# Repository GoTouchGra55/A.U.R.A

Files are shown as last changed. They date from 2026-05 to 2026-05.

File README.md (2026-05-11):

# 🚧 Under Active Development 🚧

# 

### A **flight computer** to do met- I mean math for a **rocket** (*Supposedly for a self-landing rocket*).

I had a lot of fun designing this project, though there may still be a few mistakes here and there, so forgive me for that

Feel free to suggest improvements, modify the design, or contribute your own ideas to the project as well!

---

# PCB Preview

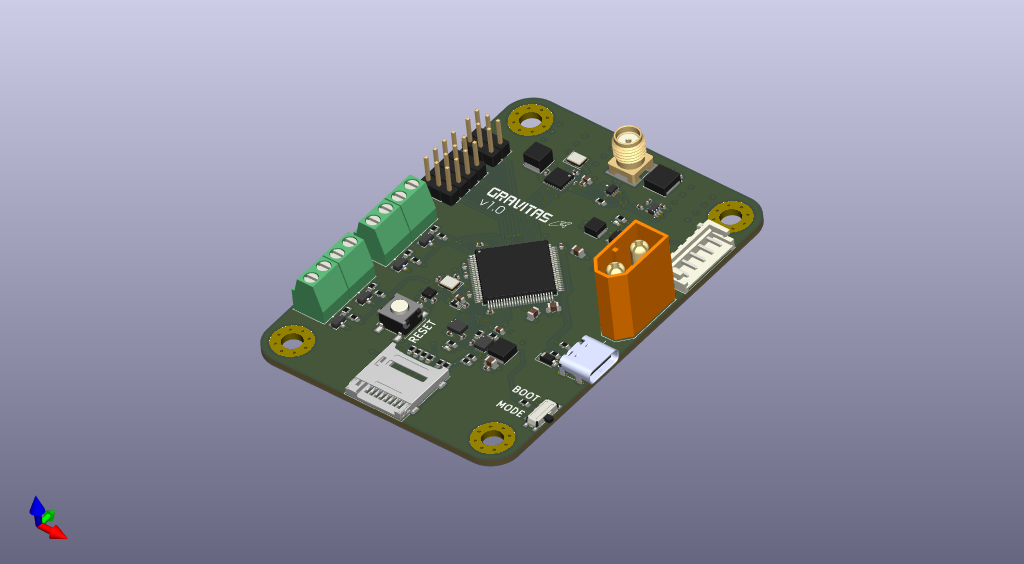
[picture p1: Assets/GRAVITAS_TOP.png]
PCB_TOP


### Yes, its 4 layers ;3

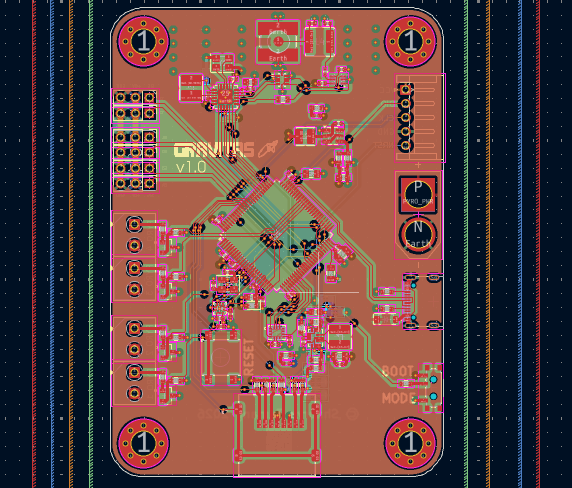
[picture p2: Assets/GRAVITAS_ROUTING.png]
PCB_ROUTES


---

# Schematics
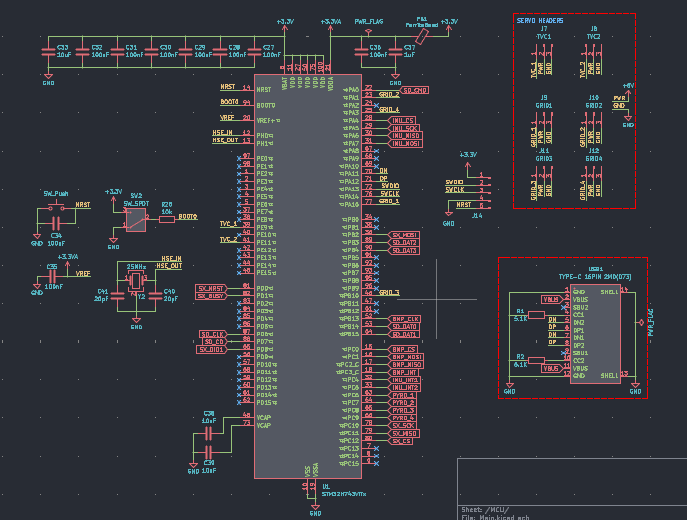
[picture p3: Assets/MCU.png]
MAIN

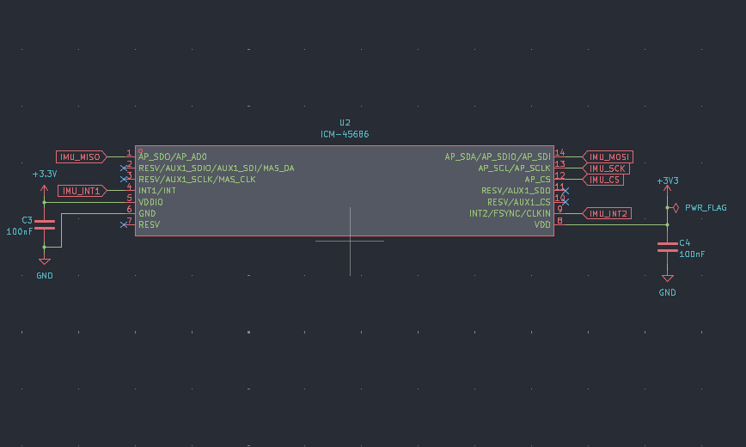
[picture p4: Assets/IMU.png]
IMU

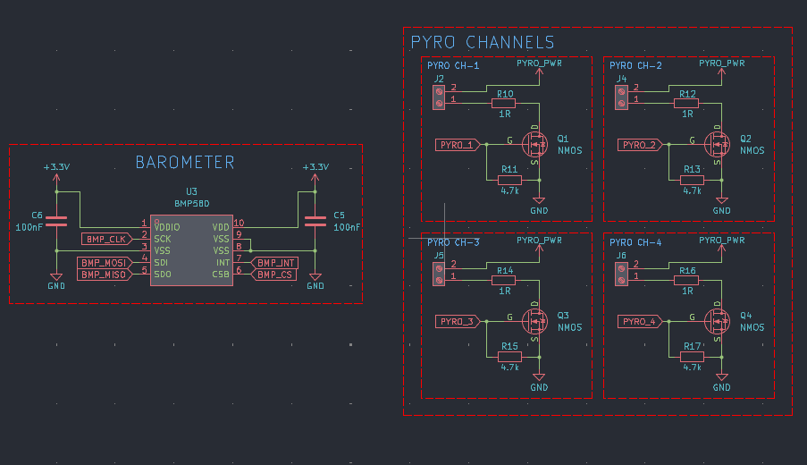
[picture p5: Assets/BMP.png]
BMP

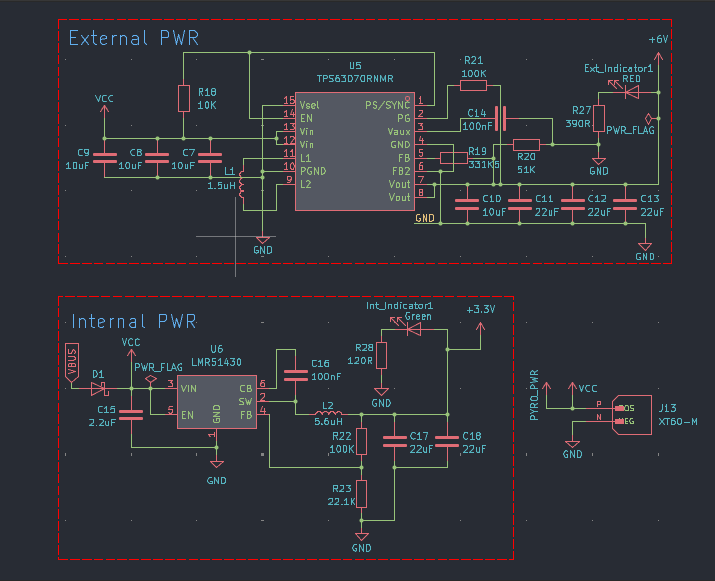
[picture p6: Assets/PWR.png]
PWR

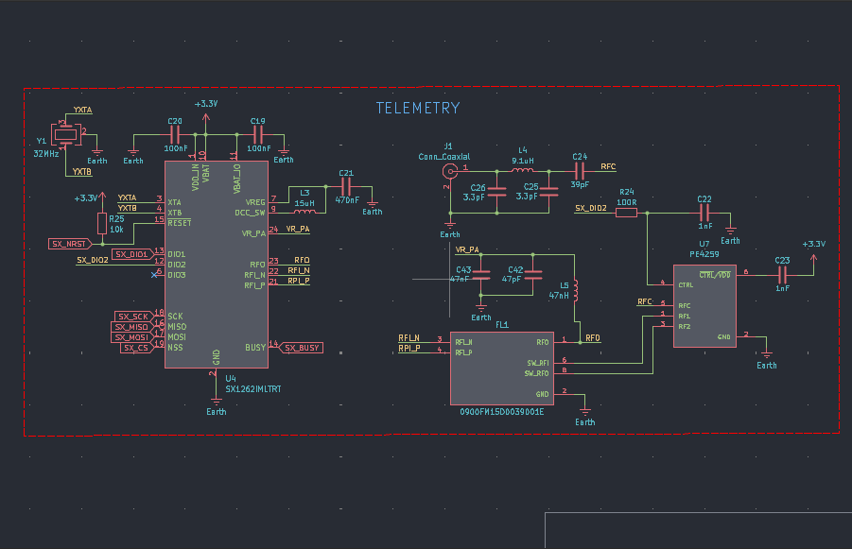
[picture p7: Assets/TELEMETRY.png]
TELEMETRY

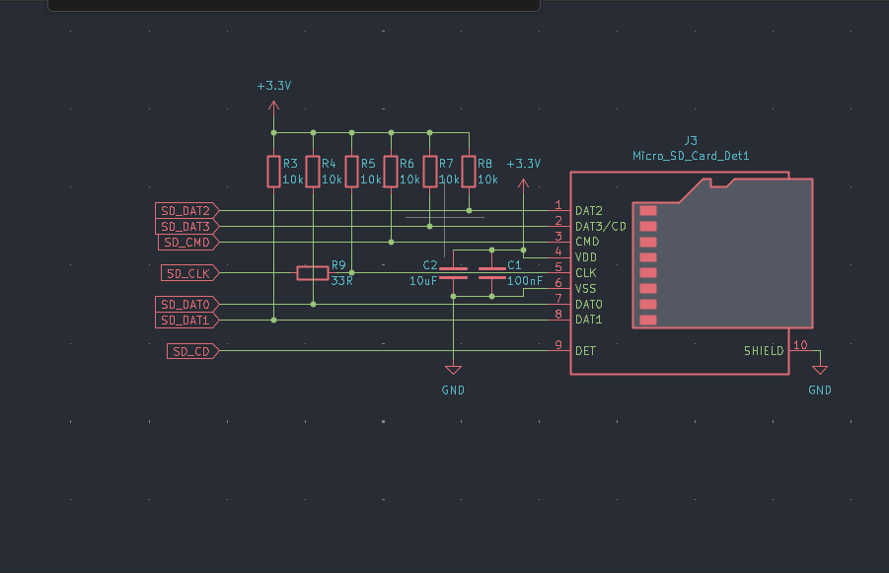
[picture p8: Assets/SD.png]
SD


---

# Extra Info

1. **Use a 2s LiPo battery** if you decide to use this board in your project. **Discard the battery if it smells "funny".**

2. **Check for any damage on the pcb** as it can be the reason for a **catastrophic failure**.

3. **USE A 915MHz SMA ANTENNA ONLY!** Others will work fine but you'll spend a while wondering about the poor range.

---

# Bill Of Materials

### See [BOM](Gravitas-bom.csv)

---

# License

### MIT License - see [LICENSE](LICENSE)

---

# Author

### **Shaurya Tamang**
Contact: shauryatamang.dev@gmail.com

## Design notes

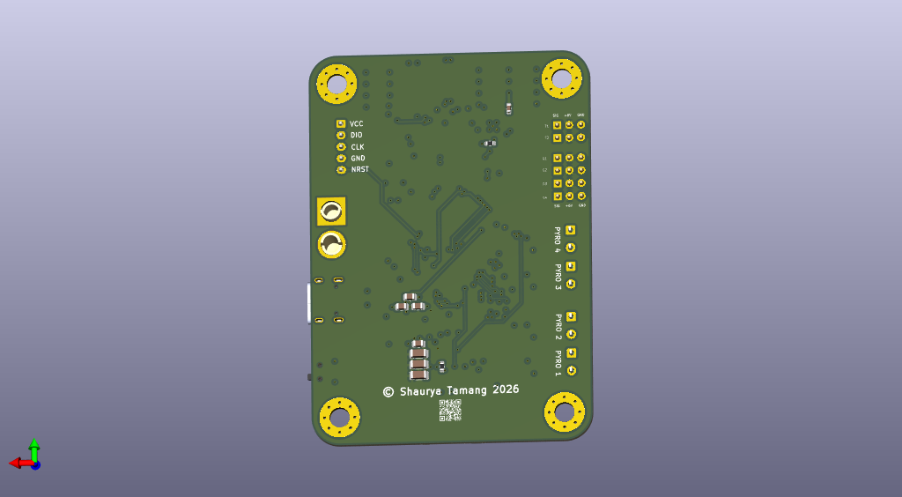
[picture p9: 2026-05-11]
Assets/GRAVITAS_BOTTOM.png

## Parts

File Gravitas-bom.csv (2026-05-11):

Name | Purpose | Quantity | Total Cost (USD) | Link | Distributor
Solder Paste | Used to solder SMD components | 1 | 4.65 | https://www.daraz.com.np/products/baku-bk-6351-bga-ic-solder-flux-paste-dispenser-i128196255-s1035314234.html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 | Daraz Nepal
Screw Terminal | Used to connect pyro charges | 1 | 0.37 | https://www.daraz.com.np/products/screw-terminal-block-connector-2pin-5pcs-i127262901-s1034506954.html?c=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 | Daraz Nepal
SMA Antenna Connector | Connector for RF Antenna | 1 | 0.93 | https://www.daraz.com.np/products/sma-female-jack-adapter-solder-edge-pcb-straight-mount-rf-copper-connector-plug-socket-i121043443-s1032975049.html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 | Daraz Nepal
SMD Capacitors | Used in circuit | 1 | 6.22 | https://www.daraz.com.np/products/320pcs-720pcs-2500pcs-0603-0805-1206-smd-capacitor-kit-assorted-kit-163650values-pumudsy-1pf-1uf-i492412636-s2210944926.html | Daraz Nepal
SMD Resistors | Used in circuit | 1 | 4.51 | https://www.daraz.com.np/products/0805-smd-resistor-kit-assorted-kit-1ohm-1m-ohm-1-33values-x-20pcs660pcs-sample-kit-0603-1206-1210-0402-10-36-80-values-i4924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 | Daraz Nepal
Flight Computer PCB | Used in rockets | 1 | 157.96 | https://cart.jlcpcb.com/shopcart/cart | JLCPCB
JLCPCB preodered parts | Used in the circuit | 1 | 17.73 | https://jlcpcb.com/user-center/smtPrivateLibrary/partsCart | JLCPCB

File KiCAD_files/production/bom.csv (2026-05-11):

Designator | Footprint | Quantity | Value | LCSC Part #
_3, _2, |  | 3
C1, C14, C16, C19, C20, C27, C28, C29, C3, C30, C31, C32, C34, C35, C36, C4, C5, C6 | 0402 | 18 | 100nF
C10, C2, C33, C38, C39, C7, C8, C9 | 0805 | 8 | 10uF
C11, C12, C13 | 1206 | 3 | 22uF
C15 | 0603 | 1 | 2.2uF
C17 | 0603 | 1 | 22uF
C18 | 0402 | 1 | 22uF
C21 | 0603 | 1 | 470nF
C22, C23 | 0402 | 2 | 1nF
C24 | 0402 | 1 | 39pF
C25, C26 | 0402 | 2 | 3.3pF
C37 | 0603 | 1 | 1uF
C40, C41 | 0402 | 2 | 20pF
C42 | 0402 | 1 | 47pF
C43 | 0603 | 1 | 47nF
D1 | D_SOD-123 | 1 | D_Schottky
EXT_INDICATOR1 | 0402 | 1 | RED
FB1 | 0603 | 1 | FerriteBead
FL1 | FIL_0900FM15D0039001E | 1 | 0900FM15D0039001E
G1 | PinHeader_1x03_P2.54mm_Vertical | 1 | GRID1
INT_INDICATOR1 | 0402 | 1 | Green
J1 | SMA_Amphenol_132134-10_Vertical | 1 | Conn_Coaxial
J10 | PinHeader_1x03_P2.54mm_Vertical | 1 | GRID2
J11 | PinHeader_1x03_P2.54mm_Vertical | 1 | GRID3
J12 | PinHeader_1x03_P2.54mm_Vertical | 1 | GRID4
J13 | AMASS_XT60-M | 1 | XT60-M
J14 | JST_EH_S5B-EH_1x05_P2.50mm_Horizontal | 1 | Conn_01x05_Pin
J2, J4, J5, J6 | TerminalBlock_Phoenix_MKDS-1-2-3.81_1x02_P3.81mm_Horizontal | 4 | Screw_Terminal_01x02
J3 | microSD_HC_Molex_47219 | 1 | Micro_SD_Card_Det1
L1 | L_Cenker_CKCS4018 | 1 | 1.5uH
L2 | L_Cenker_CKCS3015 | 1 | 5.6uH
L3 | L_Cenker_CKCS4030 | 1 | 15uH
L4 | L_Changjiang_FNR5020S | 1 | 9.1uH
L5 | 0201 | 1 | 47nH
Q1, Q2, Q3, Q4 | TRANS_IRLML6344TRPBF | 4 | NMOS
R1, R2 | 0603 | 2 | 5.1K
R10, R12, R14, R16 | 0603 | 4 | 1R
R11, R13, R15, R17 | 0603 | 4 | 4.7k
R18, R25, R26, R3, R4, R5, R6, R7, R8 | 0603 | 9 | 10K
R19 | 0603 | 1 | 331K5
R20 | 0603 | 1 | 51K
R21, R22 | 0603 | 2 | 100K
R23 | 0603 | 1 | 22.1K
R24 | 0603 | 1 | 100R
R27 | 0603 | 1 | 390R
R28 | 0603 | 1 | 120R
R9 | 0603 | 1 | 33R
SW1 | SW_SPST_B3S-1000 | 1 | SW_Push
SW2 | SW_SPDT_PCM12 | 1 | SW_SPDT
T1 | PinHeader_1x03_P2.54mm_Vertical | 1 | TVC1
T2 | PinHeader_1x03_P2.54mm_Vertical | 1 | TVC2
U1 | LQFP-100_14x14mm_P0.5mm | 1 | STM32H743VITx
U2 | IC_ICM-45686 | 1 | ICM-45686 | C22459454
U3 | ST_HLGA-10_2x2mm_P0.5mm_LayoutBorder3x2y | 1 | BMP580 | C22391138
U4 | QFN-24-1EP_4x4mm_P0.5mm_EP2.6x2.6mm | 1 | SX1262IMLTRT
U5 | VREG_TPS63070RNMR | 1 | TPS63070RNMR | C109322
U6 | SOT-23-6 | 1 | LMR51430
U7 | SOT65P215X110-6N | 1 | PE4259
USB1 | HRO_TYPE-C-31-M-12 | 1 | TYPE-C 16PIN 2MD(073) | C2765186
Y1 | Crystal_SMD_3225-4Pin_3.2x2.5mm | 1 | 32MHz
Y2 | Crystal_SMD_3225-4Pin_3.2x2.5mm | 1 | 25MHz

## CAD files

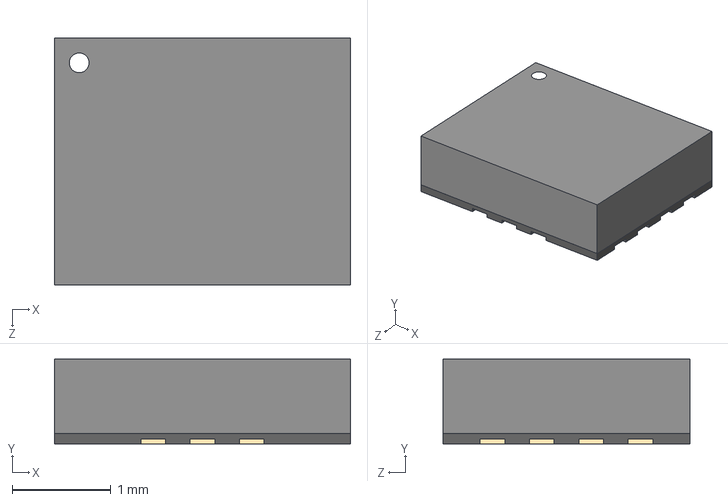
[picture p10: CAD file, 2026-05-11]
KiCAD_files/Extra_Files/ICM-45686/ICM-45686.step
3.00 x 0.86 x 2.50 mm

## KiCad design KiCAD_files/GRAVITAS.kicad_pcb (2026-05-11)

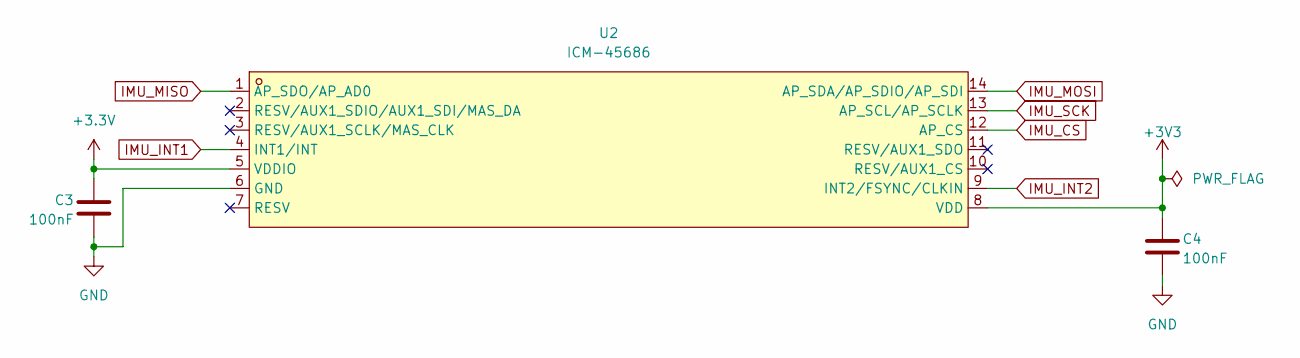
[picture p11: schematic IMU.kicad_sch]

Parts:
C3, C4: 100nF; C_0402_1005Metric
U2: ICM-45686; IC_ICM-45686; LCSC Part C22459454

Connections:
+3.3V: C3.1, U2.5 (VDDIO); also elsewhere on the board
+3V3: C4.1, U2.8 (VDD)
IMU_CS: U2.12 (AP_CS); also elsewhere on the board
IMU_INT1: U2.4 (INT1/INT); also elsewhere on the board
IMU_INT2: U2.9 (INT2/FSYNC/CLKIN); also elsewhere on the board
IMU_MISO: U2.1 (AP_SDO/AP_AD0); also elsewhere on the board
IMU_MOSI: U2.14 (AP_SDA/AP_SDIO/AP_SDI); also elsewhere on the board
IMU_SCK: U2.13 (AP_SCL/AP_SCLK); also elsewhere on the board

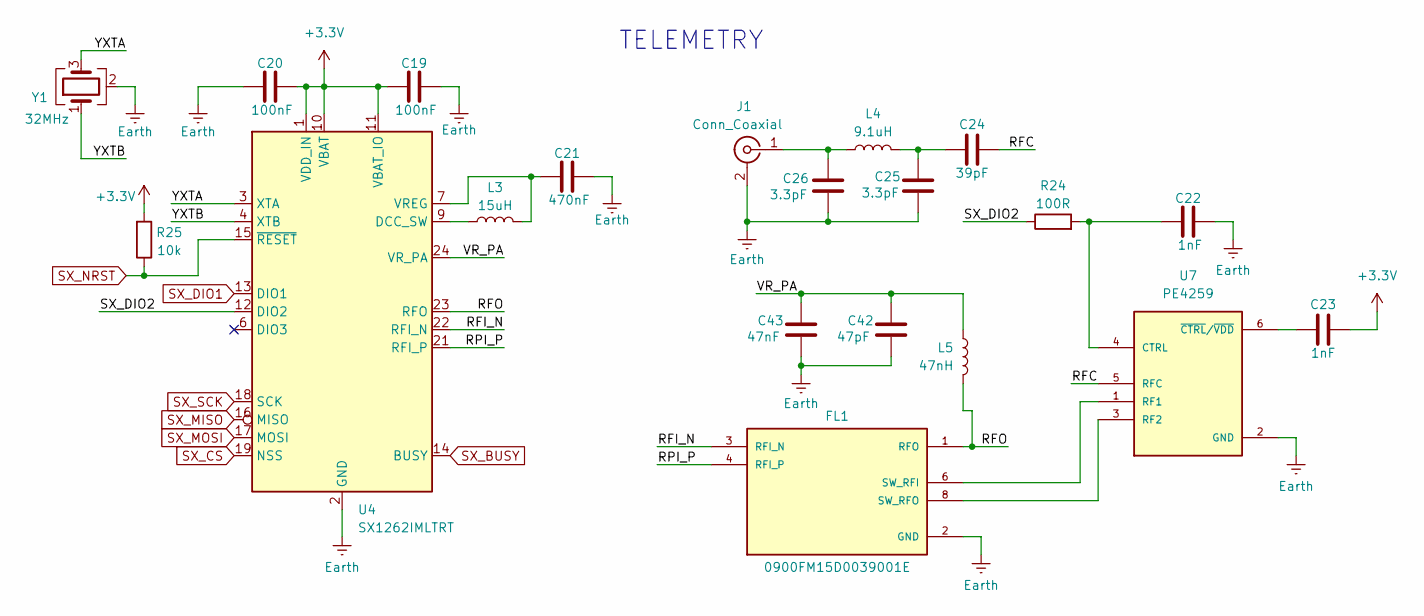
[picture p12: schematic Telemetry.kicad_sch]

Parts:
C19, C20: 100nF; C_0402_1005Metric
C21: 470nF; C_0402_1005Metric
C22, C23: 1nF; C_0603_1608Metric
C24: 39pF; C_0402_1005Metric
C25, C26: 3.3pF; C_0402_1005Metric
C42: 47pF; C_0402_1005Metric
C43: 47nF; C_0402_1005Metric
FL1: 0900FM15D0039001E; FIL_0900FM15D0039001E; PARTREV 2.0
J1: Conn_Coaxial; SMA_Amphenol_132134-10_Vertical
L3: 15uH; L_Cenker_CKCS4030
L4: 9.1uH; L_Changjiang_FNR5020S
L5: 47nH; L_0201_0603Metric
R24: 100R; R_0603_1608Metric
R25: 10k; R_0603_1608Metric
U4: SX1262IMLTRT; QFN-24-1EP_4x4mm_P0.5mm_EP2.6x2.6mm
U7: PE4259; SOT65P215X110-6N
Y1: 32MHz; Crystal_SMD_3225-4Pin_3.2x2.5mm

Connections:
+3.3V: C19.1, C20.2, C23.2, R25.2, U4.1 (VDD_IN), U4.10 (VBAT), U4.11 (VBAT_IO); also elsewhere on the board
/Telemetry/RFC: C24.1, U7.5 (RFC)
/Telemetry/RFI_N: FL1.3 (RFI_N), U4.22 (RFI_N)
/Telemetry/RFO: FL1.1 (RFO), L5.1, U4.23 (RFO)
/Telemetry/RPI_P: FL1.4 (RFI_P), U4.21 (RFI_P)
/Telemetry/SX_DIO2: R24.1, U4.12 (DIO2)
/Telemetry/VR_PA: C42.1, C43.1, L5.2, U4.24 (VR_PA)
/Telemetry/YXTA: U4.3 (XTA), Y1.3
/Telemetry/YXTB: U4.4 (XTB), Y1.1
unnamed: C24.2, C25.2, L4.1
unnamed: FL1.6 (SW_RFI), U7.1 (RF1)
unnamed: FL1.8 (SW_RFO), U7.3 (RF2)
unnamed: C26.2, J1.1 (In), L4.2
unnamed: L3.1, U4.9 (DCC_SW)
unnamed: C21.1, L3.2, U4.7 (VREG)
unnamed: C22.1, R24.2, U7.4 (CTRL)
unnamed: C23.1, U7.6 (~CTRL/~VDD)
SX_BUSY: U4.14 (BUSY); also elsewhere on the board
SX_CS: U4.19 (NSS); also elsewhere on the board
SX_DIO1: U4.13 (DIO1); also elsewhere on the board
SX_MISO: U4.16 (MISO); also elsewhere on the board
SX_MOSI: U4.17 (MOSI); also elsewhere on the board
SX_NRST: R25.1, U4.15 (~RESET); also elsewhere on the board
SX_SCK: U4.18 (SCK); also elsewhere on the board

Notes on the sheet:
TELEMETRY

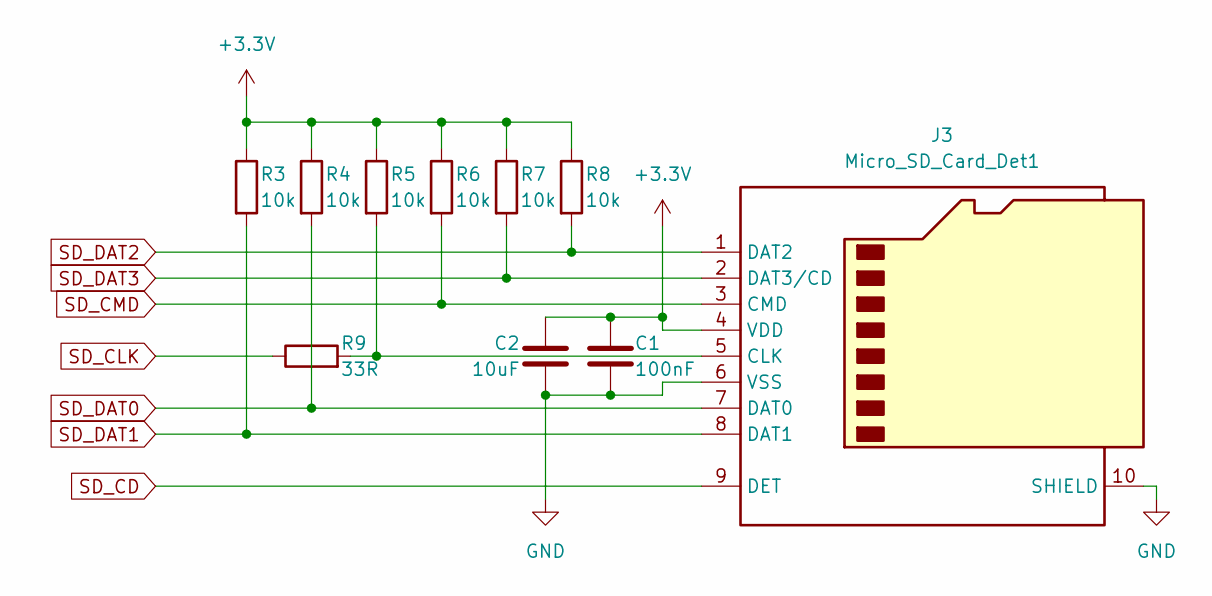
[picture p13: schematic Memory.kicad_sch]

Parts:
C1: 100nF; C_0402_1005Metric
C2: 10uF; C_0805_2012Metric
J3: Micro_SD_Card_Det1; microSD_HC_Molex_47219
R3, R4, R5, R6, R7, R8: 10k; R_0603_1608Metric
R9: 33R; R_0603_1608Metric

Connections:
+3.3V: C1.1, C2.1, J3.4 (VDD), R3.1, R4.1, R5.1, R6.1, R7.1, R8.1; also elsewhere on the board
unnamed: J3.5 (CLK), R5.2, R9.2
SD_CD: J3.9 (DET); also elsewhere on the board
SD_CLK: R9.1; also elsewhere on the board
SD_CMD: J3.3 (CMD), R6.2; also elsewhere on the board
SD_DAT0: J3.7 (DAT0), R4.2; also elsewhere on the board
SD_DAT1: J3.8 (DAT1), R3.2; also elsewhere on the board
SD_DAT2: J3.1 (DAT2), R8.2; also elsewhere on the board
SD_DAT3: J3.2 (DAT3/CD), R7.2; also elsewhere on the board

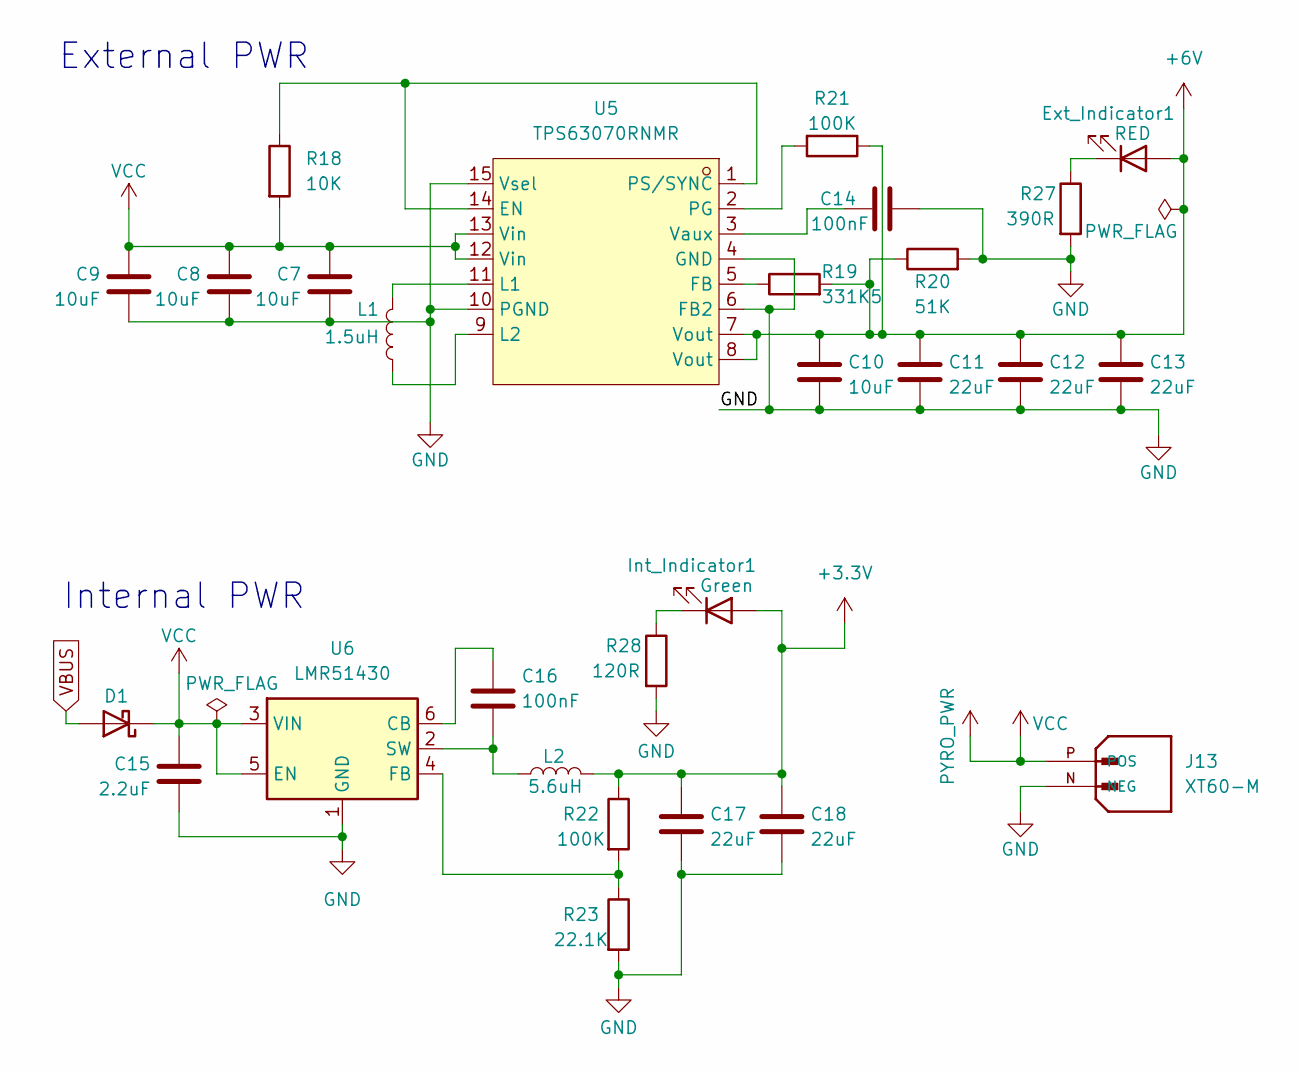
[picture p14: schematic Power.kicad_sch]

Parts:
C7, C8, C9, C10: 10uF; C_0805_2012Metric
C11, C12, C13: 22uF; C_0805_2012Metric
C14, C16: 100nF; C_0402_1005Metric
C15: 2.2uF; C_0603_1608Metric
C17, C18: 22uF; C_0603_1608Metric
D1: D_Schottky; D_SOD-123
Ext_Indicator1: RED; LED_0402_1005Metric
Int_Indicator1: Green; LED_0402_1005Metric
J13: XT60-M; AMASS_XT60-M; PARTREV V1.2
L1: 1.5uH; L_Cenker_CKCS4018
L2: 5.6uH; L_Cenker_CKCS3015
R18: 10K; R_0603_1608Metric
R19: 331K5; R_0603_1608Metric
R20: 51K; R_0603_1608Metric
R21, R22: 100K; R_0603_1608Metric
R23: 22.1K; R_0603_1608Metric
R27: 390R; R_0603_1608Metric
R28: 120R; R_0603_1608Metric
U5: TPS63070RNMR; VREG_TPS63070RNMR; LCSC Part C109322
U6: LMR51430; SOT-23-6

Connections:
+3.3V: C17.1, C18.1, Int_Indicator1.2 (A), L2.1, R22.1; also elsewhere on the board
+6V: C10.1, C11.1, C12.1, C13.1, Ext_Indicator1.2 (A), R19.2, R20.1, R21.1, U5.7 (Vout), U5.8 (Vout); also elsewhere on the board
unnamed: Ext_Indicator1.1 (K), R27.1
unnamed: Int_Indicator1.1 (K), R28.1
unnamed: R18.1, U5.1 (PS/SYNC), U5.14 (EN)
unnamed: R19.1, U5.5 (FB)
unnamed: L1.1, U5.11 (L1)
unnamed: L1.2, U5.9 (L2)
unnamed: R21.2, U5.2 (PG)
unnamed: C14.1, U5.3 (Vaux)
unnamed: C16.1, U6.6 (CB)
unnamed: R22.2, R23.1, U6.4 (FB)
unnamed: C16.2, L2.2, U6.2 (SW)
PYRO_PWR: C7.1, C8.1, C9.1, C15.1, D1.1 (K), J13.P (POS), R18.2, U5.12 (Vin), U5.13 (Vin), U6.3 (VIN), U6.5 (EN); also elsewhere on the board
VBUS: D1.2 (A); also elsewhere on the board

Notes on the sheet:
Internal PWR
External PWR

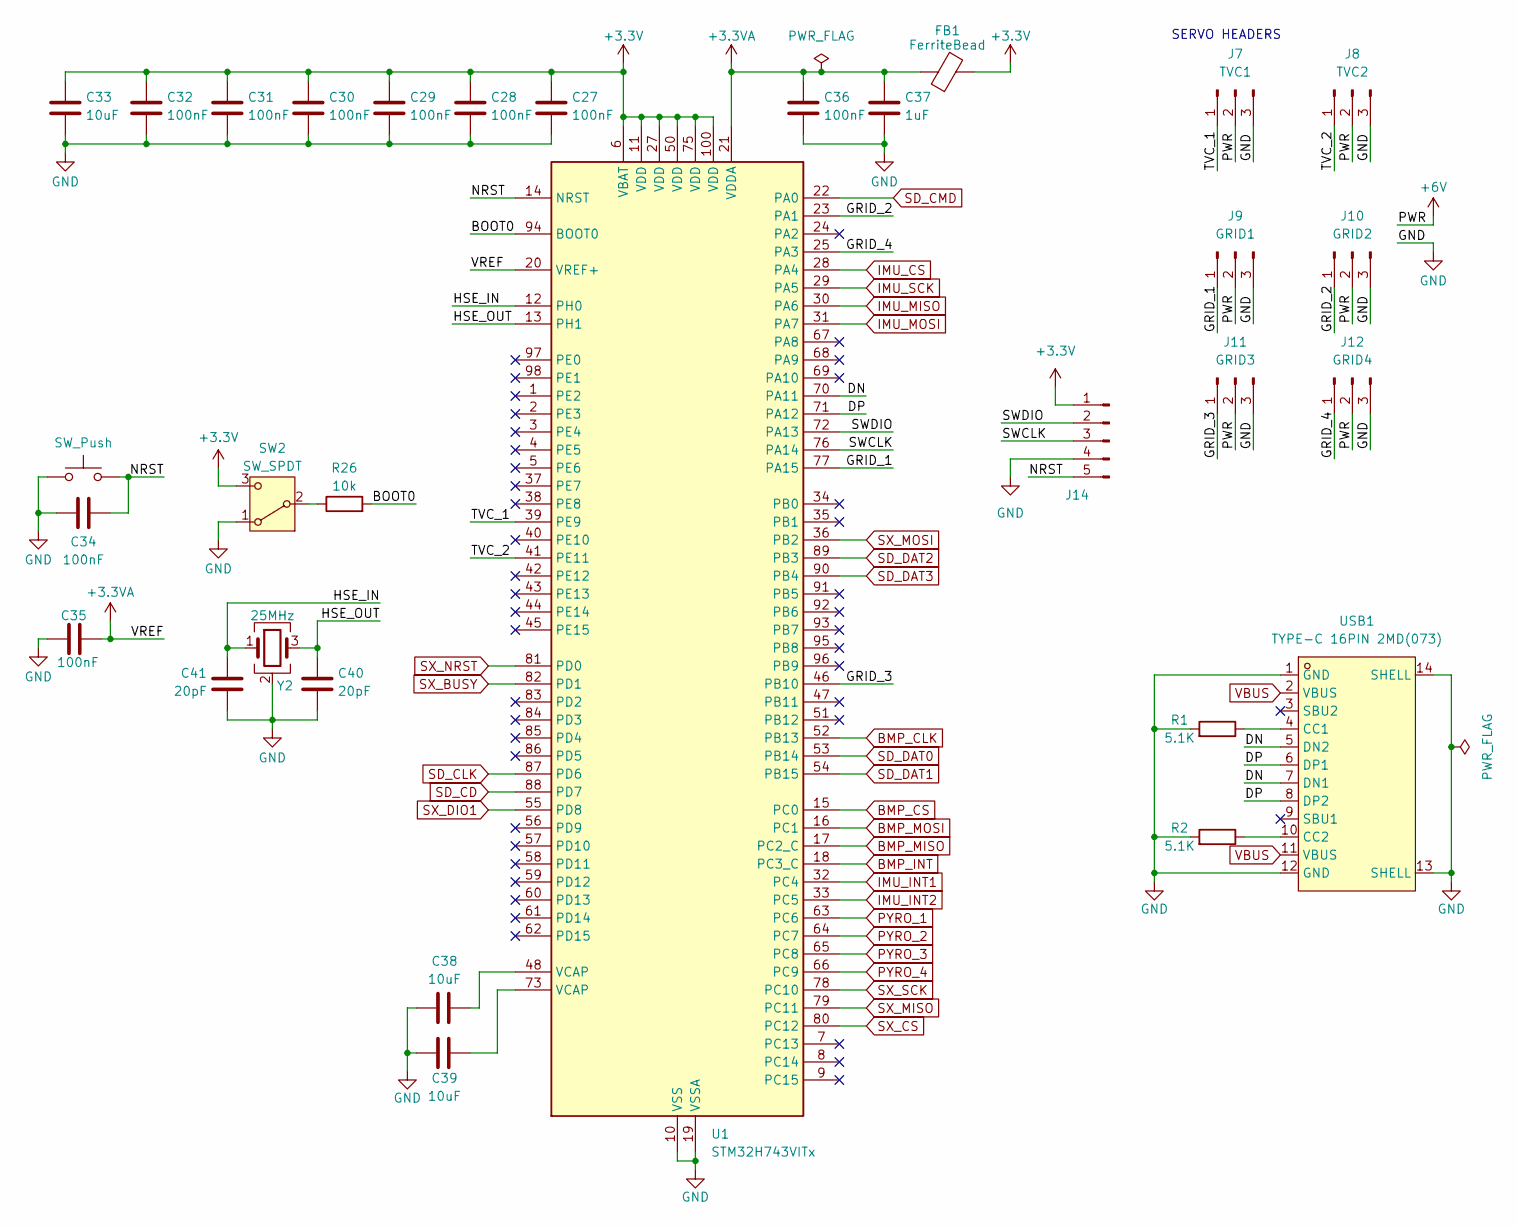
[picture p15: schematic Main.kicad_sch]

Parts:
C27, C28, C29, C30, C31, C32, C34, C35, C36: 100nF; C_0402_1005Metric
C33, C38, C39: 10uF; C_0805_2012Metric
C37: 1uF; C_0603_1608Metric
C40, C41: 20pF; C_0402_1005Metric
FB1: FerriteBead; D_0603_1608Metric
J7: TVC1; PinHeader_1x03_P2.54mm_Vertical
J8: TVC2; PinHeader_1x03_P2.54mm_Vertical
J9: GRID1; PinHeader_1x03_P2.54mm_Vertical
J10: GRID2; PinHeader_1x03_P2.54mm_Vertical
J11: GRID3; PinHeader_1x03_P2.54mm_Vertical
J12: GRID4; PinHeader_1x03_P2.54mm_Vertical
J14: Conn_01x05_Pin; JST_EH_S5B-EH_1x05_P2.50mm_Horizontal
R1, R2: 5.1K; R_0603_1608Metric
R26: 10k; R_0603_1608Metric
SW1: SW_Push; SW_SPST_B3S-1000
SW2: SW_SPDT; SW_SPDT_PCM12
U1: STM32H743VITx; LQFP-100_14x14mm_P0.5mm
USB1: TYPE-C 16PIN 2MD(073); HRO_TYPE-C-31-M-12; LCSC Part C2765186
Y2: 25MHz; Crystal_SMD_3225-4Pin_3.2x2.5mm

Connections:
+3.3V: C27.1, C28.1, C29.1, C30.1, C31.1, C32.1, C33.1, FB1.2, J14.1, SW2.3 (C), U1.6 (VBAT), U1.11 (VDD), U1.27 (VDD), U1.50 (VDD), U1.75 (VDD), U1.100 (VDD); also elsewhere on the board
+3.3VA: C35.1, C36.1, C37.1, FB1.1, U1.20 (VREF+), U1.21 (VDDA)
+6V: J7.2, J8.2, J9.2, J10.2, J11.2, J12.2; also elsewhere on the board
/MCU/BOOT0: R26.2, U1.94 (BOOT0)
/MCU/DN: U1.70 (PA11), USB1.5 (DN2), USB1.7 (DN1)
/MCU/DP: U1.71 (PA12), USB1.6 (DP1), USB1.8 (DP2)
/MCU/GRID_1: J9.1, U1.77 (PA15); also elsewhere on the board
/MCU/GRID_2: J10.1, U1.23 (PA1)
/MCU/GRID_3: J11.1, U1.46 (PB10)
/MCU/GRID_4: J12.1, U1.25 (PA3)
/MCU/HSE_IN: C41.1, U1.12 (PH0), Y2.1
/MCU/HSE_OUT: C40.1, U1.13 (PH1), Y2.3
/MCU/NRST: C34.1, J14.5, SW1.2, U1.14 (NRST)
/MCU/SWCLK: J14.3, U1.76 (PA14)
/MCU/SWDIO: J14.2, U1.72 (PA13)
/MCU/TVC_1: J7.1, U1.39 (PE9); also elsewhere on the board
/MCU/TVC_2: J8.1, U1.41 (PE11); also elsewhere on the board
BMP_CLK: U1.52 (PB13); also elsewhere on the board
BMP_CS: U1.15 (PC0); also elsewhere on the board
BMP_INT: U1.18 (PC3_C); also elsewhere on the board
BMP_MISO: U1.17 (PC2_C); also elsewhere on the board
BMP_MOSI: U1.16 (PC1); also elsewhere on the board
IMU_CS: U1.28 (PA4); also elsewhere on the board
IMU_INT1: U1.32 (PC4); also elsewhere on the board
IMU_INT2: U1.33 (PC5); also elsewhere on the board
IMU_MISO: U1.30 (PA6); also elsewhere on the board
IMU_MOSI: U1.31 (PA7); also elsewhere on the board
IMU_SCK: U1.29 (PA5); also elsewhere on the board
unnamed: C38.2, U1.48 (VCAP)
unnamed: C39.1, U1.73 (VCAP)
unnamed: R26.1, SW2.2 (B)
unnamed: R1.1, USB1.4 (CC1)
unnamed: R2.1, USB1.10 (CC2)
PYRO_1: U1.63 (PC6); also elsewhere on the board
PYRO_2: U1.64 (PC7); also elsewhere on the board
PYRO_3: U1.65 (PC8); also elsewhere on the board
PYRO_4: U1.66 (PC9); also elsewhere on the board
SD_CD: U1.88 (PD7); also elsewhere on the board
SD_CLK: U1.87 (PD6); also elsewhere on the board
SD_CMD: U1.22 (PA0); also elsewhere on the board
SD_DAT0: U1.53 (PB14); also elsewhere on the board
SD_DAT1: U1.54 (PB15); also elsewhere on the board
SD_DAT2: U1.89 (PB3); also elsewhere on the board
SD_DAT3: U1.90 (PB4); also elsewhere on the board
SX_BUSY: U1.82 (PD1); also elsewhere on the board
SX_CS: U1.80 (PC12); also elsewhere on the board
SX_DIO1: U1.55 (PD8); also elsewhere on the board
SX_MISO: U1.79 (PC11); also elsewhere on the board
SX_MOSI: U1.36 (PB2); also elsewhere on the board
SX_NRST: U1.81 (PD0); also elsewhere on the board
SX_SCK: U1.78 (PC10); also elsewhere on the board
VBUS: USB1.2 (VBUS), USB1.11 (VBUS); also elsewhere on the board

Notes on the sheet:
SERVO HEADERS

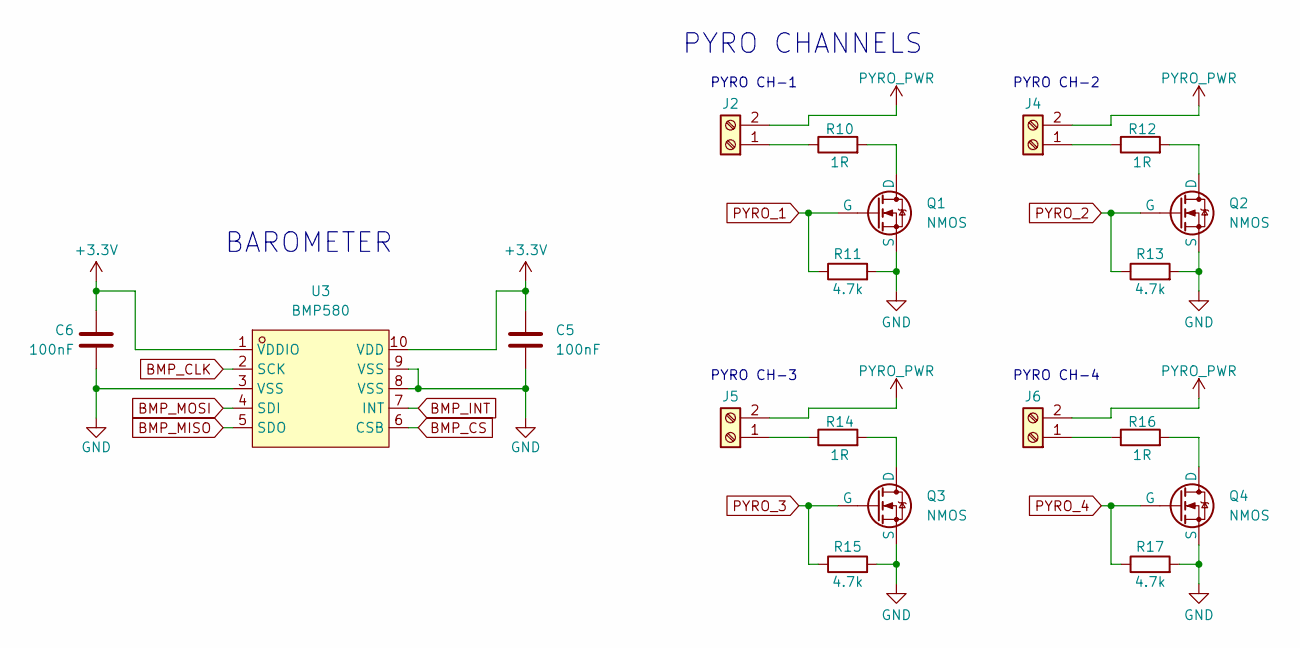
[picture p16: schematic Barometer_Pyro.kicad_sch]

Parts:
C5, C6: 100nF; C_0402_1005Metric
J2, J4, J5, J6: Screw_Terminal_01x02; TerminalBlock_Phoenix_MKDS-1-2-3.81_1x02_P3.81mm_Horizontal
Q1, Q2, Q3, Q4: NMOS; TRANS_IRLML6344TRPBF
R10, R12, R14, R16: 1R; R_0603_1608Metric
R11, R13, R15, R17: 4.7k; R_0603_1608Metric
U3: BMP580; ST_HLGA-10_2x2mm_P0.5mm_LayoutBorder3x2y; LCSC Part C22391138

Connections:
+3.3V: C5.1, C6.1, U3.1 (VDDIO), U3.10 (VDD); also elsewhere on the board
BMP_CLK: U3.2 (SCK); also elsewhere on the board
BMP_CS: U3.6 (CSB); also elsewhere on the board
BMP_INT: U3.7 (INT); also elsewhere on the board
BMP_MISO: U3.5 (SDO); also elsewhere on the board
BMP_MOSI: U3.4 (SDI); also elsewhere on the board
unnamed: J2.1, R10.1
unnamed: J4.1, R12.1
unnamed: J5.1, R14.1
unnamed: J6.1, R16.1
unnamed: Q1.1 (D), R10.2
unnamed: Q2.1 (D), R12.2
unnamed: Q3.1 (D), R14.2
unnamed: Q4.1 (D), R16.2
PYRO_1: Q1.2 (G), R11.1; also elsewhere on the board
PYRO_2: Q2.2 (G), R13.1; also elsewhere on the board
PYRO_3: Q3.2 (G), R15.1; also elsewhere on the board
PYRO_4: Q4.2 (G), R17.1; also elsewhere on the board
PYRO_PWR: J2.2, J4.2, J5.2, J6.2; also elsewhere on the board

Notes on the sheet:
PYRO CHANNELS
PYRO CH-3
PYRO CH-4
BAROMETER
PYRO CH-2
PYRO CH-1

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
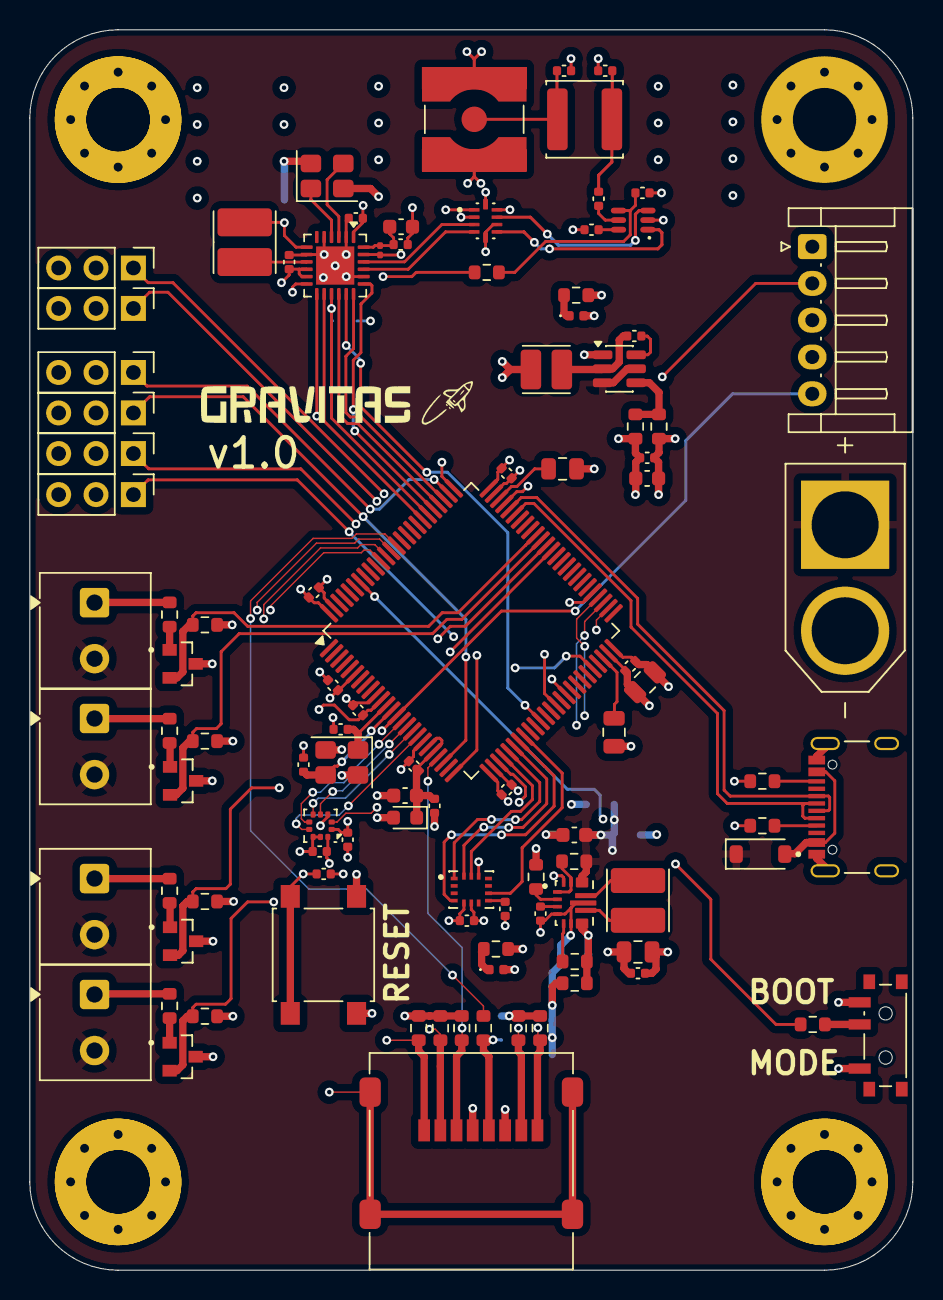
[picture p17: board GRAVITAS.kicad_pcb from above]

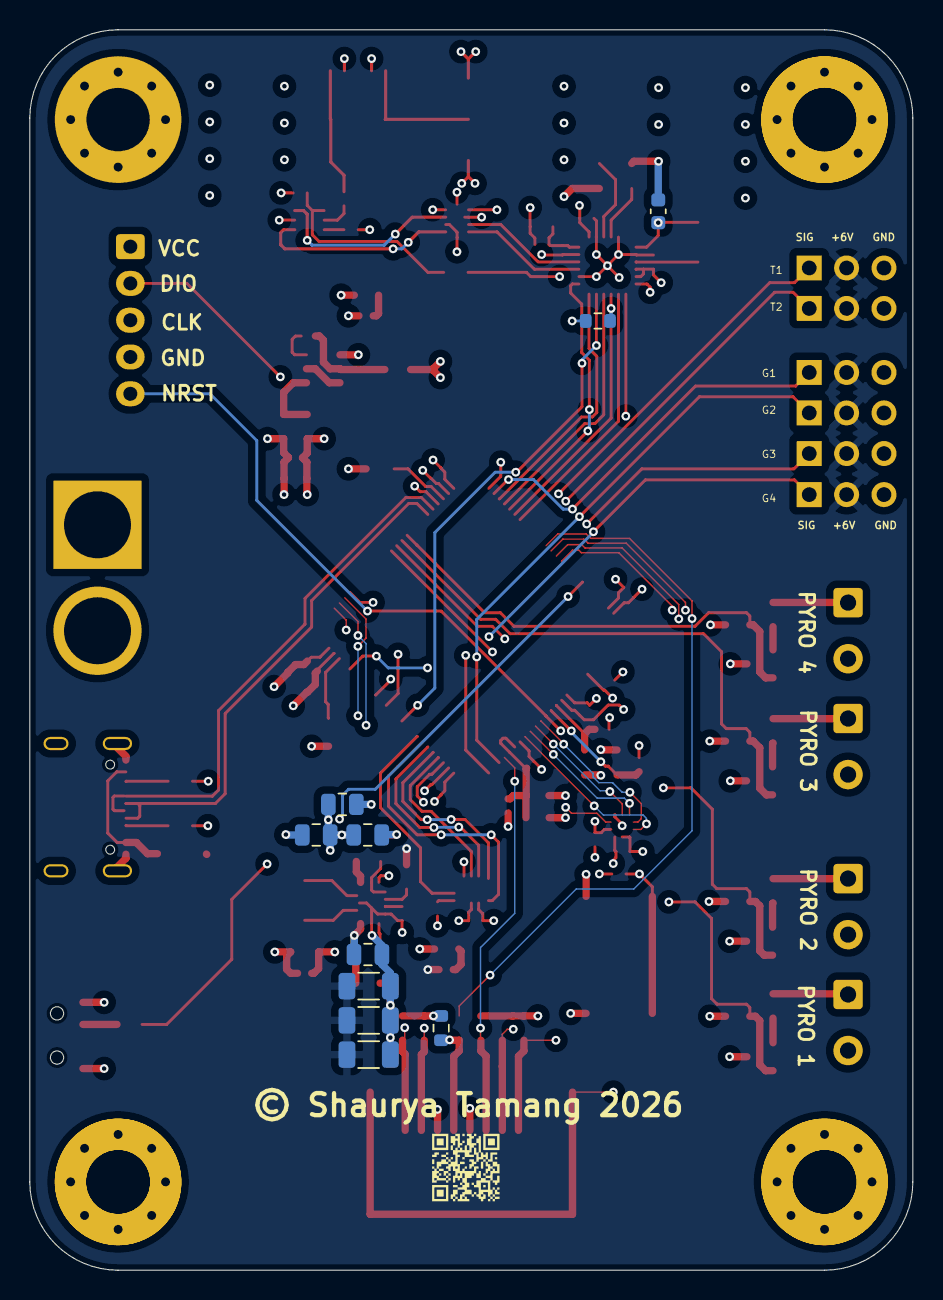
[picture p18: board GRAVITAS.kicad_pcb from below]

Board: 4 copper layers, 60.0 x 84.3 mm, 111 parts (10 on the bottom side), 91 nets.

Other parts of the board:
G1: GRID1; PinHeader_1x03_P2.54mm_Vertical
T1: TVC1; PinHeader_1x03_P2.54mm_Vertical
T2: TVC2; PinHeader_1x03_P2.54mm_Vertical

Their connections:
+6V: G1.2, T1.2, T2.2; also elsewhere on the board
/MCU/GRID_1: G1.1; also elsewhere on the board
/MCU/TVC_1: T1.1; also elsewhere on the board
/MCU/TVC_2: T2.1; also elsewhere on the board

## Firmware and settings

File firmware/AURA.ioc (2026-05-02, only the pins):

Mcu.UserName=STM32H743VITx
PA0.Signal=SDMMC2_CMD
PA1.Signal=S_TIM2_CH2
PA11.Signal=USB_OTG_FS_DM
PA12.Signal=USB_OTG_FS_DP
PA2.GPIO_Label=IMU_INT1
PA2.Signal=GPXTI2
PA3.Signal=S_TIM2_CH4
PA4.GPIO_Label=IMU_CS
PA4.Signal=GPIO_Output
PA5.GPIO_Label=IMU_SCK
PA5.Signal=SPI1_SCK
PA6.GPIO_Label=IMU_MISO
PA6.Signal=SPI1_MISO
PA7.GPIO_Label=IMU_MOSI
PA7.Signal=SPI1_MOSI
PB10.Signal=S_TIM2_CH3
PB13.GPIO_Label=BMP_SCK
PB13.Signal=SPI2_SCK
PB14.Signal=SDMMC2_D0
PB15.Signal=SDMMC2_D1
PB2.GPIO_Label=SX_MOSI
PB2.Signal=SPI3_MOSI
PC0.GPIO_Label=BMP_CS
PC0.Signal=GPIO_Output
PC1.GPIO_Label=BMP_MOSI
PC1.Signal=SPI2_MOSI
PC10.GPIO_Label=SX_SCK
PC10.Signal=SPI3_SCK
PC11.GPIO_Label=SX_MISO
PC11.Signal=SPI3_MISO
PC12.GPIO_Label=SX_CS
PC12.Signal=GPIO_Output
PC2_C.GPIO_Label=BMP_MISO
PC2_C.Signal=SPI2_MISO
PC3_C.GPIO_Label=BMP_INT
PC3_C.Signal=GPXTI3
PD0.GPIO_Label=SX_NRST
PD0.Signal=GPIO_Output
PD6.Signal=SDMMC2_CK
PD7.GPIO_Label=SD_CD
PD7.Signal=GPIO_Input
PE11.Signal=S_TIM1_CH2
PE9.Signal=S_TIM1_CH1

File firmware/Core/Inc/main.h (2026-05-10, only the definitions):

#define BMP_CS_Pin GPIO_PIN_0
#define BMP_CS_GPIO_Port GPIOC
#define BMP_MOSI_Pin GPIO_PIN_1
#define BMP_MOSI_GPIO_Port GPIOC
#define BMP_MISO_Pin GPIO_PIN_2
#define BMP_MISO_GPIO_Port GPIOC
#define BMP_INT_Pin GPIO_PIN_3
#define BMP_INT_GPIO_Port GPIOC
#define GRID_CH2_Pin GPIO_PIN_1
#define GRID_CH2_GPIO_Port GPIOA
#define GRID_CH4_Pin GPIO_PIN_3
#define GRID_CH4_GPIO_Port GPIOA
#define IMU_CS_Pin GPIO_PIN_4
#define IMU_CS_GPIO_Port GPIOA
#define IMU_SCK_Pin GPIO_PIN_5
#define IMU_SCK_GPIO_Port GPIOA
#define IMU_MISO_Pin GPIO_PIN_6
#define IMU_MISO_GPIO_Port GPIOA
#define IMU_MOSI_Pin GPIO_PIN_7
#define IMU_MOSI_GPIO_Port GPIOA
#define IMU_INT1_Pin GPIO_PIN_4
#define IMU_INT1_GPIO_Port GPIOC
#define IMU_INT2_Pin GPIO_PIN_5
#define IMU_INT2_GPIO_Port GPIOC
#define SX_MOSI_Pin GPIO_PIN_2
#define SX_MOSI_GPIO_Port GPIOB
#define TVC_CH1_Pin GPIO_PIN_9
#define TVC_CH1_GPIO_Port GPIOE
#define TVC_CH2_Pin GPIO_PIN_11
#define TVC_CH2_GPIO_Port GPIOE
#define GRID_CH3_Pin GPIO_PIN_10
#define GRID_CH3_GPIO_Port GPIOB
#define BMP_SCK_Pin GPIO_PIN_13
#define BMP_SCK_GPIO_Port GPIOB
#define PYRO_CH1_Pin GPIO_PIN_6
#define PYRO_CH1_GPIO_Port GPIOC
#define PYRO_CH2_Pin GPIO_PIN_7
#define PYRO_CH2_GPIO_Port GPIOC
#define PYRO_CH3_Pin GPIO_PIN_8
#define PYRO_CH3_GPIO_Port GPIOC
#define PYRO_CH4_Pin GPIO_PIN_9
#define PYRO_CH4_GPIO_Port GPIOC
#define GRID_CH1_Pin GPIO_PIN_15
#define GRID_CH1_GPIO_Port GPIOA
#define SX_SCK_Pin GPIO_PIN_10
#define SX_SCK_GPIO_Port GPIOC
#define SX_MISO_Pin GPIO_PIN_11
#define SX_MISO_GPIO_Port GPIOC
#define SX_CS_Pin GPIO_PIN_12
#define SX_CS_GPIO_Port GPIOC
#define SX_NRST_Pin GPIO_PIN_0
#define SX_NRST_GPIO_Port GPIOD
#define SX_BUSY_Pin GPIO_PIN_1
#define SX_BUSY_GPIO_Port GPIOD
#define SD_CD_Pin GPIO_PIN_7
#define SD_CD_GPIO_Port GPIOD

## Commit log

2026-05-11 Add KiCAD files
    [Barometer.kicad_sch, Barometer_Pyro.kicad_sch, GRAVITAS.kicad_pcb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]
2026-05-11 Update README and add files
    [Gravitas-bom.csv]

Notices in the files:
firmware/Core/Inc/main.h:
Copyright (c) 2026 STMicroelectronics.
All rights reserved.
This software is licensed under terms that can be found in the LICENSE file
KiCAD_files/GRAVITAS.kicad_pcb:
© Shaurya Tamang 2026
